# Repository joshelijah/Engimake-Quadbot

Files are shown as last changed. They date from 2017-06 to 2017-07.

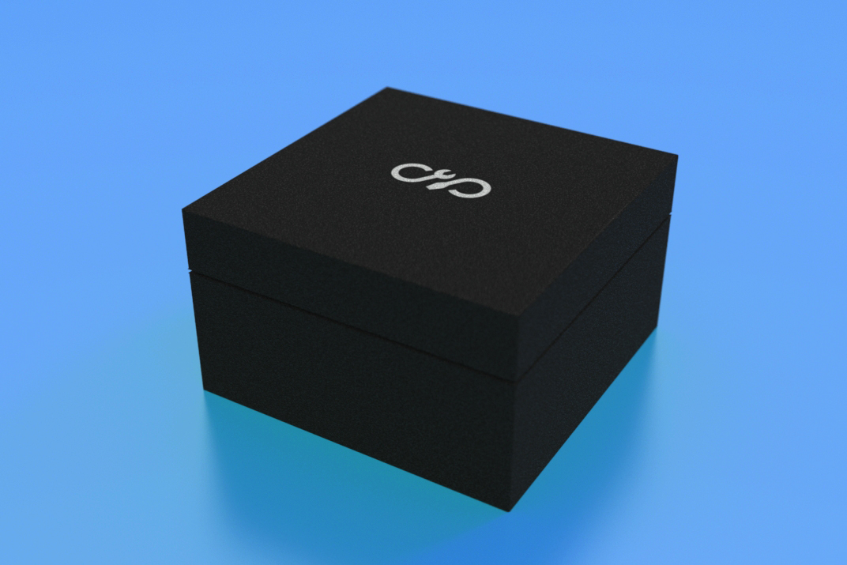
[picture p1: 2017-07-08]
Images/package design mockup.JPG

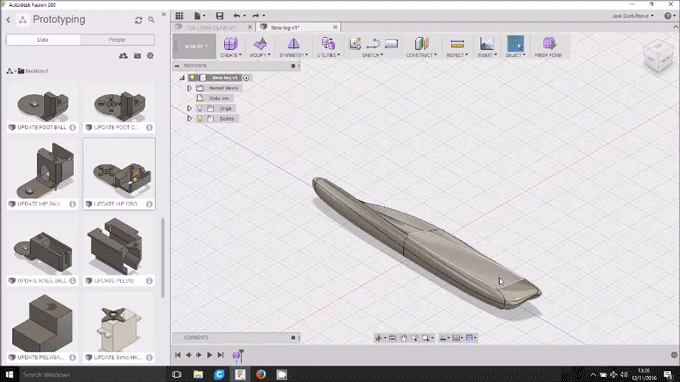
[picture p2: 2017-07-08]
Images/3D-Design.gif

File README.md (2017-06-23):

# Engimake-Quadbot
The design and software files for the Engimake QuadBot. An open source, four-legged, 3D Printed robot. Included here are all the files you'll need to create QuadBot.

1) The Arduino code
2) The Mechanical design files
3) The PCB layout

These files are presented as-is, and are not in a finished state. You'll need to apply initiative to fill in any gaps, this is not a step by step guide! That said these files are the basis of what you'll need to build a working QuadBot.Producing  / manufacturing or creating an object from any of the included design files is expressly at your own risk.

## Getting Started

These instructions will tell you what software you'll need for accessing these design and software files. 

### Prerequisites

What things you need to install the software and how to install them

```
Software: Arduino IDE, found here (www.arduino.cc/en/Main/Software)
Mechanical Design: Any 3D CAD package. We used Autodesk Fusion 360, found here (www.autodesk.com/products/fusion-360/free-trial)
Electronics Design: Any electronics CAD package. We recommend DesignSpark PCB or Eagle (www.rs-online.com/designspark/pcb-software) or (https://www.autodesk.com/products/eagle/free-download)

```

### Installing Arduino

Installing the CAD packages is straight forward. To program QuadBot from Arduino you will need to install Arduino and the following Arduino libraries...

```
1) The Servo library
2) The Adafruit Neopixel library, found here (https://github.com/adafruit/Adafruit_NeoPixel)
3) The QuadBot library, found in these files.
```
The Servo library comes preinstalled with Arduino, and allows us to control the servos. The Adafruit Neopixel library needs to be downloaded and installed to Arduino. Follow the link below for a guide on installing Arduino libraries.

https://www.arduino.cc/en/Guide/Libraries

The QuadBot library was written by us to allow easy programming of QuadBot. It's relatively straight forward and well documented. Credit to Daniel Elijah for writing this fantastic library. d.elijah@gmail.com

```
1) Install the Arduino IDE. 
2) Download the Adafruit Neopixel library and install it.
3) Download the QuadBot library and install it.
```

## Built With

* [Autodesk Fusion 360](www.autodesk.com/products/fusion-360/free-trial) - CAD software
* [DesignSpark PCB](www.rs-online.com/designspark/pcb-software) - Electronics Cad software
* [Arduino](www.arduino.cc/en/Main/Software) - Arduino

## Contributing

Feel free as you wish to contribute your designs. This repository is not maintained.

## Authors

Engimake Ltd.

## License

This project is licensed under the Creative Commons Attribution-ShareAlike 4.0 International License (CC BY-SA 4.0). Refer to http://creativecommons.org/licenses/by-sa/4.0/ for more information.

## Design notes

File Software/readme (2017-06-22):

##QuadBot Library Files

Place these files in your Arduino library file to install the QuadBot.h Arduino library.

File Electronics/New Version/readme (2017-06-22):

Electronics

Included here are the PCB gerber files that will be needed to manufacture a QuadBoard.

Also included is the Bill of Materials for all components on the board.

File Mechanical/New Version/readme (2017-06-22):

Mechanical Files

Find the QuadBot mechanical files here.

All files are suitable for 3D printing. 

All components are in .f3d and .iges format.

We recommend using Autodesk Fusion 360 for the files.

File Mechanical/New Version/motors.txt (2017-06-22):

The motors used for QuadBot are...

Feetech FS90 servo.

You can buy them from multiple places, including...

https://www.pololu.com/product/2818
https://www.rapidonline.com/feetech-fs90r-360-continuous-rotation-micro-servo-37-1335
https://grobotronics.com/servo-micro-1.5kg.cm-plastic-gears-feetech-fs90.html

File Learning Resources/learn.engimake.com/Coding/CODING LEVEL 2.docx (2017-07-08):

LEFT SIDEBAR | MAIN CONTENT
IMAGE
TITLE: CODING LEVEL 2
BLURB: Take your coding knowledge to the next level!
LEFT MENU: The Arduino Environment, The Arduino Language, What is a Library?, Anatomy of an Arduino Sketch, Conclusion

URL: engimake.com/coding/l2/0

The Arduino Environment (H1)

If you want to get set up and running, check out our the getting started guide. Here we’ll learn about the Arduino environment

The Arduino programming language is what we use to program QuadBot. Arduino is a huge platform with a large user base and lots of example code. It forms the core of every program we’ll write for QuadBot.

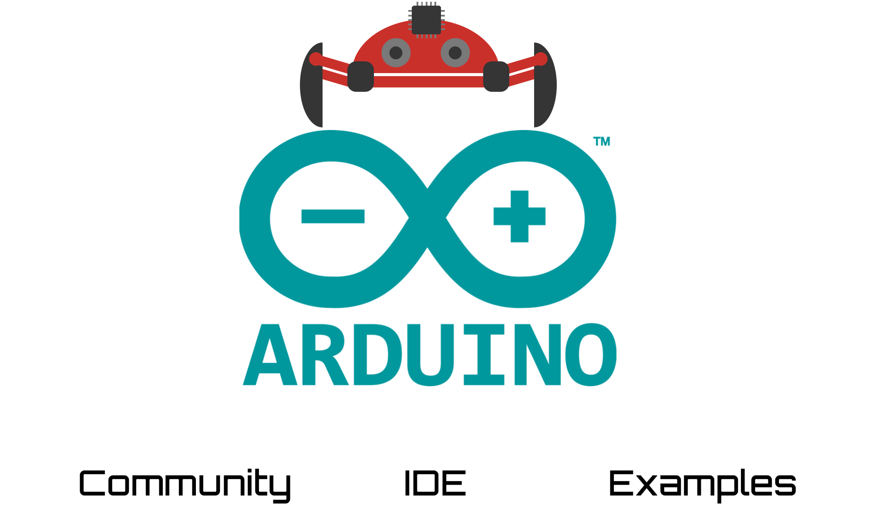
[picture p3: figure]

But what actually is the Arduino language? Let’s take a look.
RIGHT BUTTON TEXT: NONE URL | LEFT BUTTON TEXT: The Arduino Language URL: engimake.com/coding/l2/1

URL: engimake.com/coding/l2/1

The Arduino Language (H1)

Arduino is based on the C++ language, which has been around since 1983. The normal C++ used with microcontrollers but can be a bit complicated.

The Arduino language makes C++ a lot easier because it gives you loads of software libraries containing pre-written functions. This means if you want to perform a specific operation it’s likely there’s a function already existing for you to use.

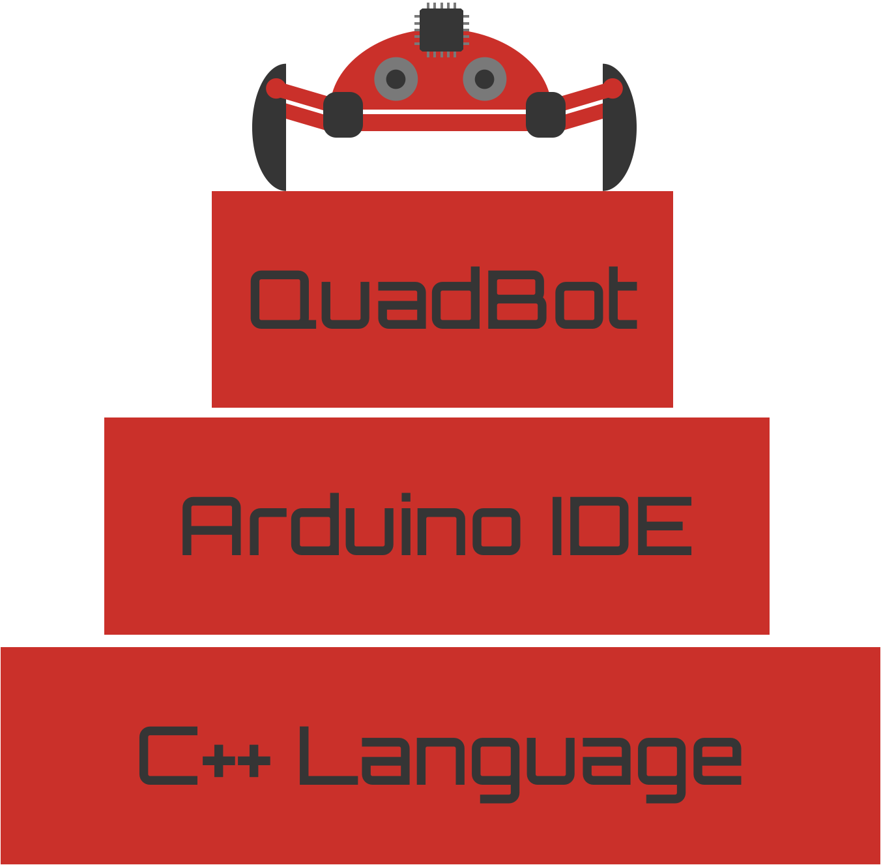
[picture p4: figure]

QuadBot is built from the Arduino Integrated Development Environment (IDE). The Arduino IDE is built from the C++ Language.
RIGHT BUTTON TEXT: The Arduino environment URL: engimake.com/coding/l2/0 | LEFT BUTTON TEXT: What is a library? URL: engimake.com/coding/l2/2

URL: engimake.com/coding/l2/2

What is a Library (H1)

A software library is just a big list of functions written by someone else. They’ve done all the hard work of creating the function and getting it work, so that we can use the function in our programs. Why? Because coders are pretty awesome people.

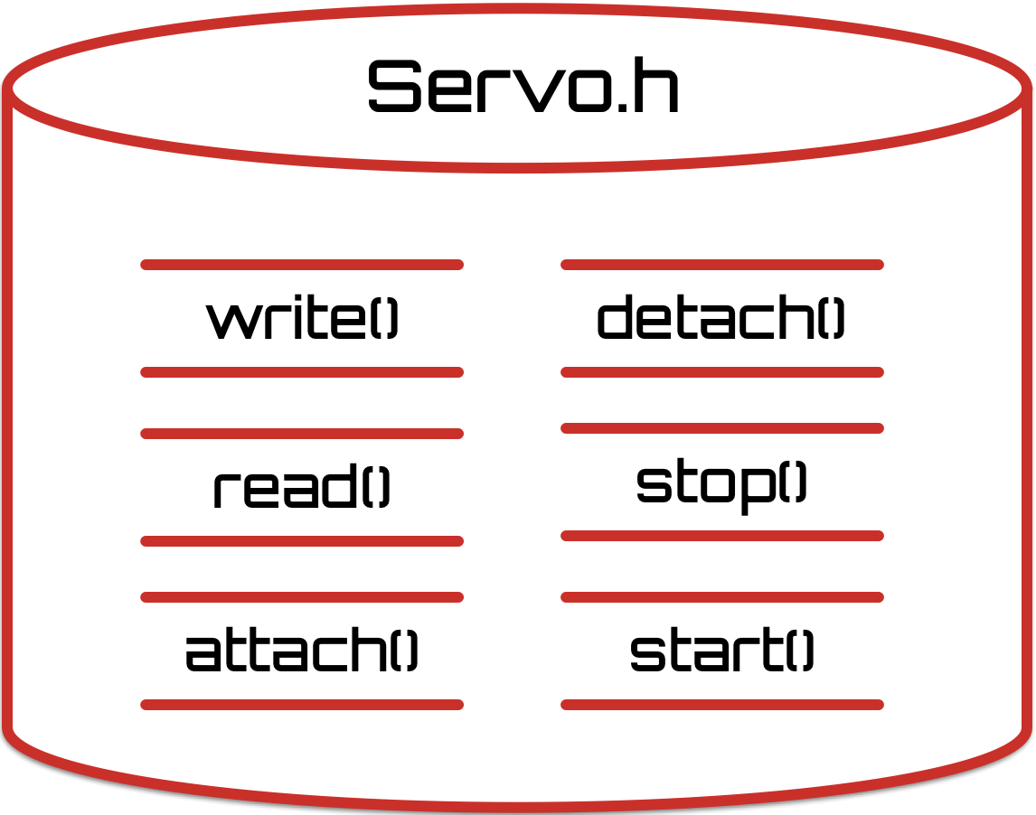
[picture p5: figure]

Think of a library as like a container for a load of functions that all relate to one thing. For example here we’ve got the Servo library, which relates to Servo motors. The library contains functions to stop and start the servo, amongst others.

There are a LOT of different libraries for arduino, some are official and well documented, others are unofficial and bit hacky.

To include a library in our code, we use the following statement at the top of our program…

#include <Servo.h>

RIGHT BUTTON TEXT: The Arduino language URL: engimake.com/coding/l2/1 | LEFT BUTTON TEXT: Anatomy of an Arduino sketch URL: engimake.com/coding/l2/3

URL: engimake.com/coding/l2/3

Anatomy of an Arduino sketch (H1)

All Arduino sketches consist of two parts, setup() and loop(). The setup() runs once at the start, the loop() runs continuously.

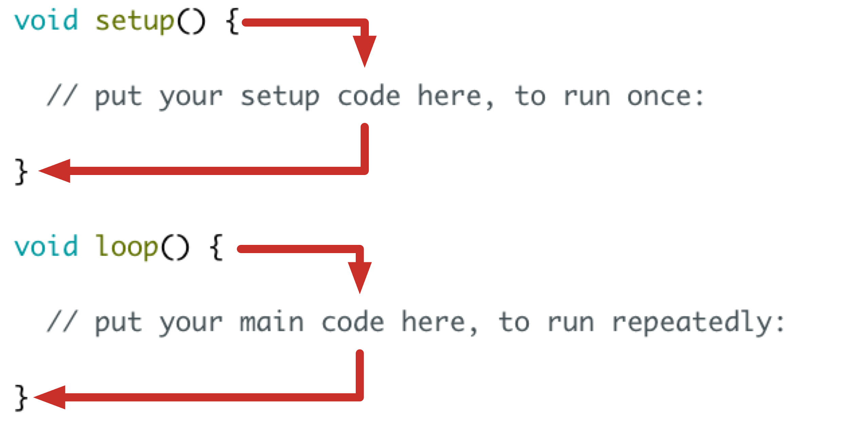
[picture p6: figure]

You’ll use the setup() for things like setting up pins as inputs or outputs. These only happen once. You’ll use the loop() to run your main code.

Here’s an Arduino sketch in all its glory.

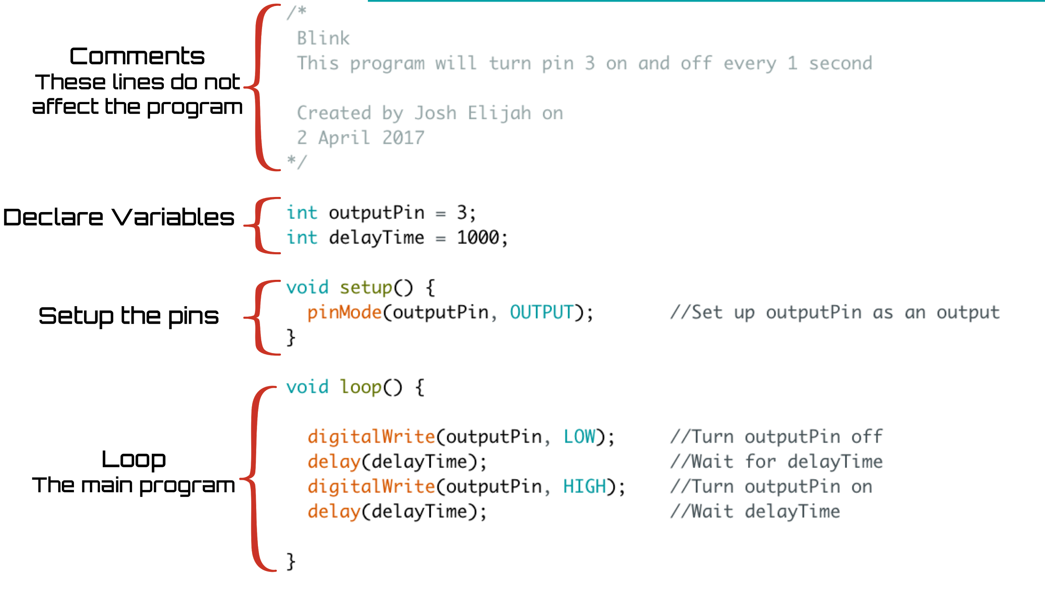
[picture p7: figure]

Comments: These do not affect the program, they are there to help humans understand the code.

Declare Variables: We declare any variables here at the start of the program.

Setup: We setup the pin as an output. We only need to do this once at the start, so it goes in setup().

Loop: Inside here is the code we want to repeat, turning the pin on and off.
RIGHT BUTTON TEXT: What is a library URL: URL: engimake.com/coding/l2/2 | LEFT BUTTON TEXT: Conclusion URL: URL: engimake.com/coding/l2/4

URL: engimake.com/coding/l2/4

Conclusion (H1)

Now you’re getting very familiar with the Arduino language. Continue on to learn more about coding, or head over to our get started guides to get QuadBot moving!
RIGHT BUTTON TEXT: Anatomy of an Arduino sketch URL: engimake.com/coding/l2/3 | LEFT BUTTON TEXT: URL

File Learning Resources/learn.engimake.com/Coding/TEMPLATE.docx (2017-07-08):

LEFT SIDEBAR | MAIN CONTENT | RIGHT SIDEBAR

RIGHT BUTTON TEXT URL | LEFT BUTTON TEXT URL

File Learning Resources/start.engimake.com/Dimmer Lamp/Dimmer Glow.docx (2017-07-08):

Left Sidebar

Create a dimmable lamp with QuadBot

Overview

Analog Input

Reading the Dial

The Map Function

Combining what we know

Difficulty rating: 3

Fun Rating: 3

Time taken: 25 mins

Supporting activity - QuadBot Colour

Dimmer Control

Master analog input and LED control to create a dimmable lamp with QuadBot.

Dimmable LEDs GIF

There’s a handy dial on QuadBot that we can program to control any of features. In this activity you’ll program the dial to control the brightness of LEDs. First let’s look at analog input.

Analog Input

QuadBot can sense analog voltages between 0 volts and 5 volts using its onboard microcontroller. Coincidentally, the dial onboard QuadBot outputs a voltage between 0 volts and 5 volts depending on the position it is in. That means we can use the dial to send different voltages to QuadBot’s microcontroller, allowing us to input a varying value.

Varying voltage from dial photo (with graphic overlay)

The microcontroller reads this voltage as a number between 0 and 1023. 0 volts means 0, and 5 volts means 1023. This might seem a bit strange, and it’s down to how microcontrollers store the voltage information.

Why does a microcontroller read an analog voltage as a number between 0 and 1023? Read our Input and Output tutorial.

Now we know that let’s look at how to actually use this…

Reading the dial

We can use the readDial() function from the QuadBot.h library to return the current value of the dial, like this…

#include <QuadBot.h> //Include the QuadBot Library

int dial; //Declare a variable to store the value of the dial

void setup(){

QuadBot.begin() //Initialize QuadBot

}

void loop(){

dial = QuadBot.readDial() //Read the value of the dial and store it in “dial”

}

The readDial() function returns the value from the dial (between 0 and 1023) We can use this variable in our code to make decisions.

To use this value to control the LED brightness, we’ll need to give the value into the QuadBot.setLEDs(R,G,B) function.

There’s a problem though. We know that readDial() returns a value between 0 and 1023, however we know that setLEDs() expects values for R,G and B between 0 and 255! To solve this problem we can use the map() function...

The Map Function

The Map function is one of those sort of functions you just can’t live without. It’s built into the Arduino environment and you can read about it in detail Arduino’s page here (https://www.arduino.cc/en/reference/map). The map function takes one number from one range, and scales it into another number from another range.

To understand this, let’s take an example. Say I’ve got a grade of 0.73 out of a range between 0 and 1. How can I express that as a grade between 0 and 100. This is simple, we can just multiple the original grade by 100. So 0.73 between 0 and 1 is equivalent to 73 between 0 and 100. That’s a very simple mapping.

But how can we do this for more complicated mappings?

- Map 34 from range 5-85 to range 0 to 100
- Map 0.1 from range -4 to 4 to range 80 to 90
- Map 512 from range 0 to 1023 to range 0 to 255

We could go through the math, but we don’t have to, we can use the Arduino map() function. The function takes five inputs and returns the new, mapped value. We use it like this…

int newVal = map(oldVal, oldLow, oldHigh, newLow, newHigh);

So to map value “dial” in the range of 0 to 1023, to the range of 0 to 255 we do the following.

map(dial, 0, 1023, 0, 255);

Combining what we know

Let’s bring it all together to create our dimmer switch. Let’s read the dial, map the value, then use it to set the LEDs…

#include <QuadBot.h> //Include the QuadBot Library

int dial; //Declare a variable to store the value of the dial

int level; // Declare a variable to store the brightness value

void setup(){

QuadBot.begin() //Initialize QuadBot

}

void loop(){

dial = QuadBot.readDial() //Read the value of the dial and store it in “dial”

level = map(dial, 0,1023, 0,255); //map the value to bet

setLEDs(level, level, level); //Set the brightness according to the level

}

And hurrah! You’ve now created a white dimmer lamp with QuadBot. Try using some maths to increase/decrease the brightness values for R, G and B. That way you can create a colored dimmer lamp!

Conclusion

Now you’re getting somewhere! Well done, you’ve combined input with output and are ready to move on to some more advanced concepts, go you!

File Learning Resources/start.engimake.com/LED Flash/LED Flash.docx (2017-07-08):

Left Sidebar

The Arduino equivalent of “Hello World!”

Overview

Digital Output

Conclusion

Difficulty rating: 1

Fun Rating: 1

Time taken: 10 mins

Dimmer Control

Understand basic programming and digital output by flashing the onboard LED.

Fl LEDs GIF

There’s a small LED on QuadBot that’s hooked up directly to one of the digital pins on the microcontroller. In this most simple exercise let’s make it flash

There’s a handy dial on QuadBot that we can program to control any of features. In this activity you’ll program the dial to control the brightness of LEDs. First let’s look at analog input.

Digital Output

There are two voltage levels when it comes to a digital output pin, High and Low. High means 5V and Low means 0V on QuadBot. When the digital pin 3 is high, an LED on QuadBot turns on. When digital pin 3 is low, the LED turns off. Simples.

What is a digital signal? Read our Input and Output tutorial.

To toggle the voltage on this pin we can use the digitalWrite() function like this…

void setup(){

pinMode(3, OUTPUT);

}

void loop(){

digitalWrite(3, HIGH); //Send out a HIGH on digital pin 3

digitalWrite(3, LOW); //Send out a HIGH on digital pin 3

}

You expect to see the LED flashing right? But if you tried it, you’d see that the LED is constantly on? Why?

Well the microcontroller runs very quickly at up to 16 million operations per second. That means that even though the LED is being turned on and off, it is so quick we can’t see it. To solve this let’s use the delay() function to make the microcontroller wait between each toggle..

void setup(){

pinMode(3, OUTPUT);

}

void loop(){

digitalWrite(3, HIGH); //Send out a HIGH on digital pin 3

delay(1000); //Wait for 1 second

digitalWrite(3, LOW); //Send out a HIGH on digital pin 3

delay(1000); //Wait for 1 second

}

Now you’ll see a second delay between each toggle. Try changing the delay times and see what it does to the flashing LED.

Conclusion

Now that’s a start. That’s your most basic microcontroller introduction. Now move onto something more exciting!

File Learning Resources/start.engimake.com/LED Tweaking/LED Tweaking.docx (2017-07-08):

Left Sidebar

Let’s tweak the LEDs one by one to get custom patterns

Overview

Editing our motor tweak code

Difficulty rating: 4

Fun Rating: 4

Time taken: 25 mins

Supporting activity - Motor Tweaking

LED Tweaking

Get manual control over all the LEDs and be able to tweak them individually using the dial.

LED tweaking

Let’s adapt our motor tweaking code to tweak each LED individually...

Editing our motor Tweak code

This is very simple, let’s simply replace the motor code with LED code...

int newButtonState = LOW;

int oldButtonState = LOW;

int numberOfPresses = 0;

int LEDnumber = 0;

int dial;

long color;

void setup() {

QuadBot.begin();

}

void loop() {

newButtonState = QuadBot.readButton(); //Read the value of button

if (newButtonState != oldButtonState) { //If the button is different to its previous value…

if(newButtonState == LOW){ //If the button has just been pressed, the value should be LOW

numberOfPresses++; //Increment the number of presses

}

}

delay(50);

oldButtonState = newButtonstate; //Assign the current button state to be the old button state for the next loop.

LEDnumber = numberOfPresses%8 //Take the modulo 8 of numberOfPresses

dial = map(QuadBot.readDial(),0,1023,0,255);

color = colorWheel(dial);

QuadBot.writeLED(LEDnumber, angle); //Set the angle of the motor to the mapped dial value

}

And that’s it, the same as before but now with LEDs

Conclusion

Very simple, let’s move on!

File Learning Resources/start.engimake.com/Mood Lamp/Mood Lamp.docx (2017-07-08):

Left Sidebar

Add color control to your dimmable QuadBot lamp.

Overview

Reading the button and setting the color

Setting the brightness

Difficulty rating: 3

Fun Rating: 4

Time taken: 25 mins

Supporting activity - QuadBot Color

Color Controlled Dimmer

Upgrade the dimmable QuadBot lamp so that you can control not only the brightness, but the color as well.

Dimmable and Color variable LEDs GIF

We’ll combine using the dial and the button on QuadBot to let use the dial to set either the brightness or the color of the QuadBot. First let’s adapt our previous code to make the color change only when the button is pressed.

Add button read into our previous code

We can use the readButton() function to decide whether to change the color of the LEDs. We use a new function here called colorWheel() that converts a number from 0 to 255 into a color on the color wheel.

#include <QuadBot.h> //Include the QuadBot Library

long color; //A variable to store the color value

int dial; //A variable to store the value of the dial

void setup(){

QuadBot.begin() //Initialize QuadBot

}

void loop(){

dial = map(analogRead(A0),0,1023,0,255); //Map dial value to maximum 255

if(QuadBot.readButton()){ //If the button is pressed

color = colorWheel(dial); //Set dial to be the colorwheel position of dial

writeLEDs(color); //Set the color of the LEDs using the color wheel

}

}

Now whenever you press the button, you should be able to change the color by turning the dial!

Setting the brightness

Finally let’s make the dial control the LED brightness when the button isn’t pressed. We can just add an else statement to our code, that runs when the button isn’t pressed!

#include <QuadBot.h> //Include the QuadBot Library

long color; //A variable to store the color value

int dial; //A variable to store the value of the dial

void setup(){

QuadBot.begin() //Initialize QuadBot

}

void loop(){

dial = map(analogRead(A0),0,1023,0,255); //Map dial value to maximum 255

if(QuadBot.readButton()){ //If the button is pressed

color = colorWheel(dial); //Set dial to be the colorwheel position of dial

writeLEDs(color); //Set the color of the LEDs using the color wheel

}

else{

setLEDsBrightness(dial); //Set the brightness of the LEDs

}

delay(1) //Add a small loop delay

}

And now you should be able to get the exact color and brightness you want on QuadBot! Great work!

Conclusion

Fantastic progress! You’re starting to combine multiple inputs and make decisions for outputs. This is the essense of robotics! Let’s try some of the other outputs on QuadBot!

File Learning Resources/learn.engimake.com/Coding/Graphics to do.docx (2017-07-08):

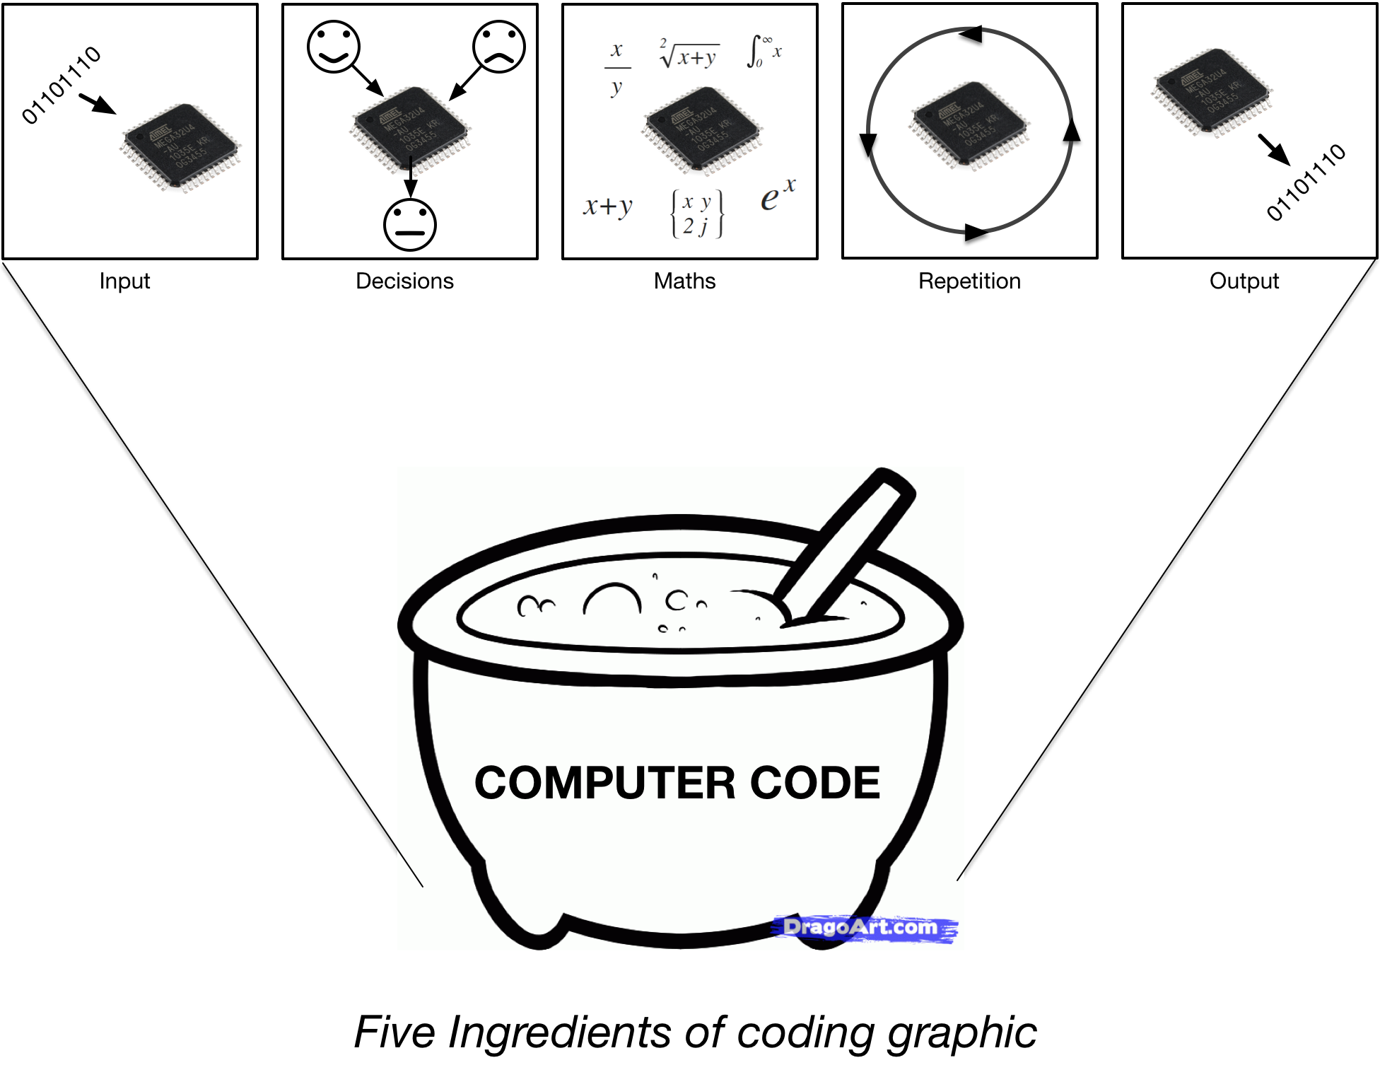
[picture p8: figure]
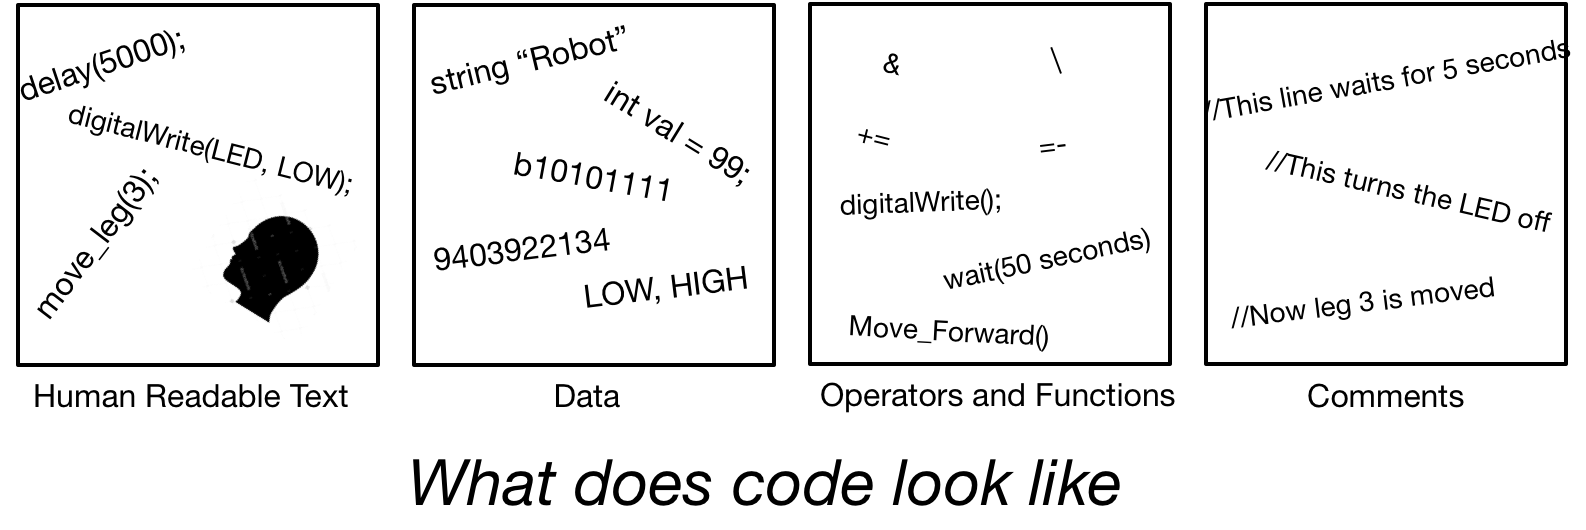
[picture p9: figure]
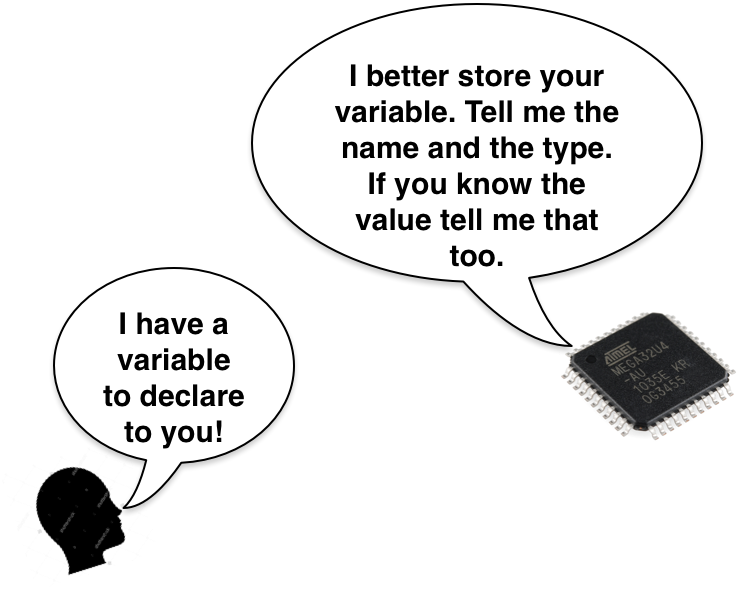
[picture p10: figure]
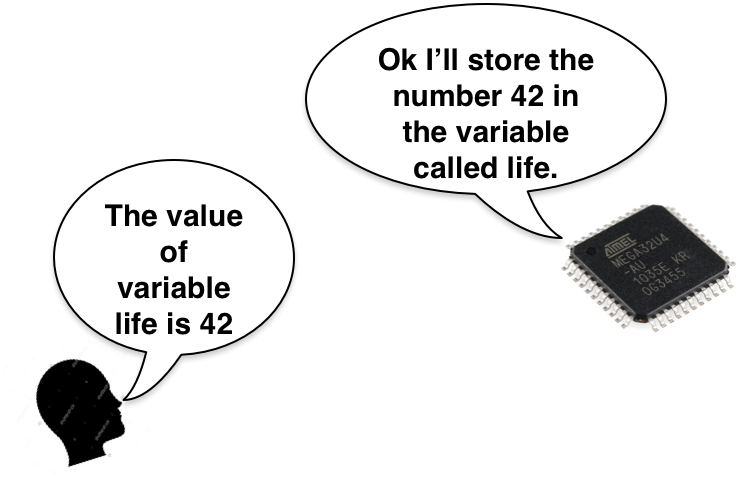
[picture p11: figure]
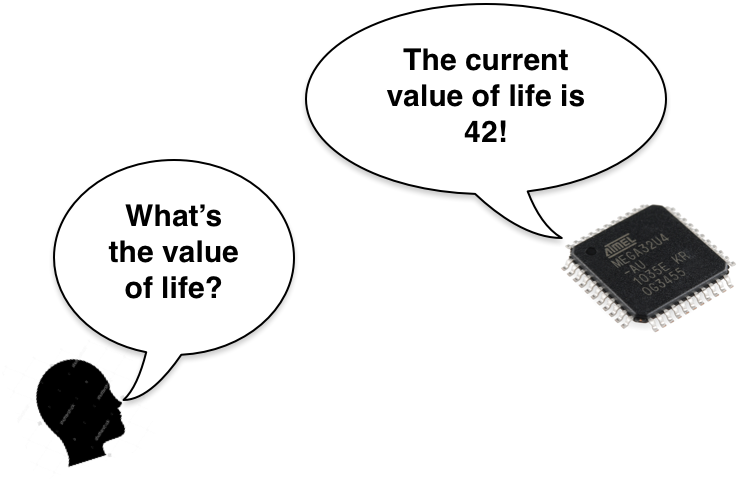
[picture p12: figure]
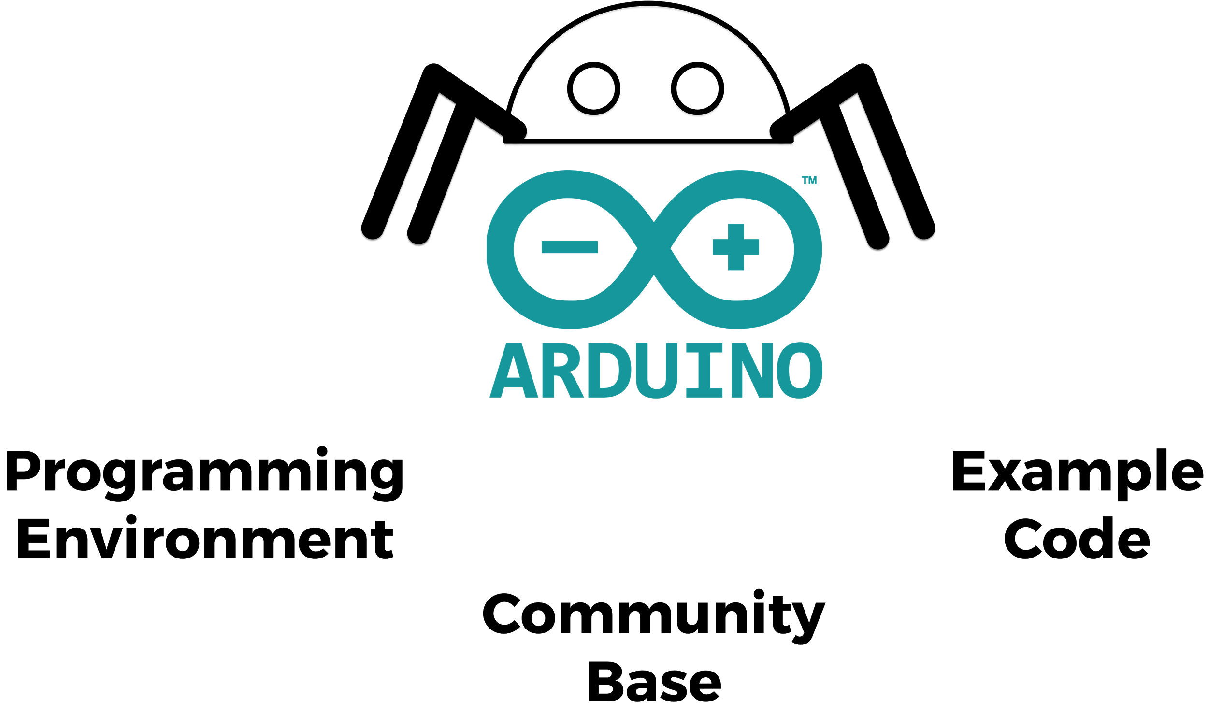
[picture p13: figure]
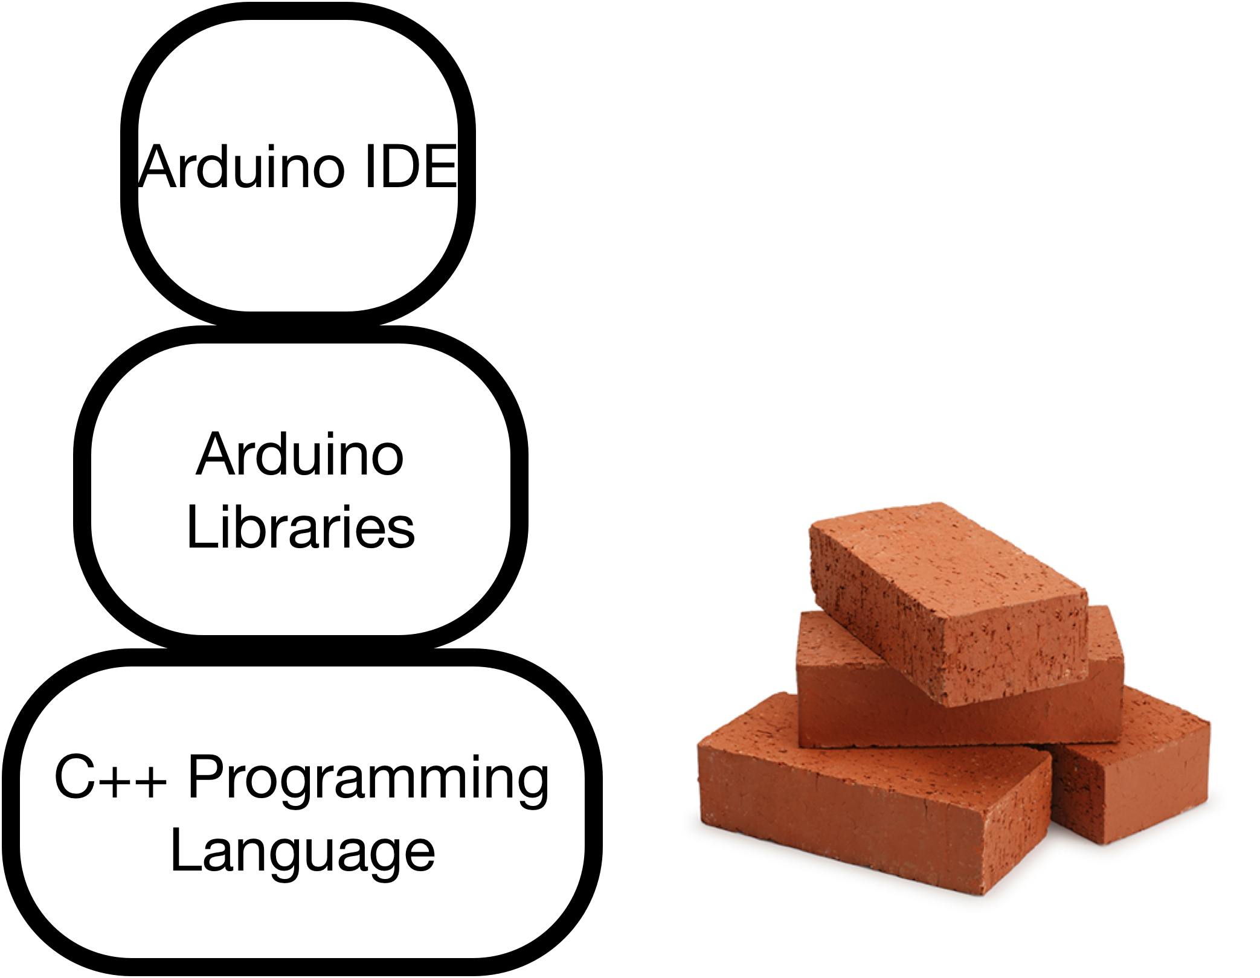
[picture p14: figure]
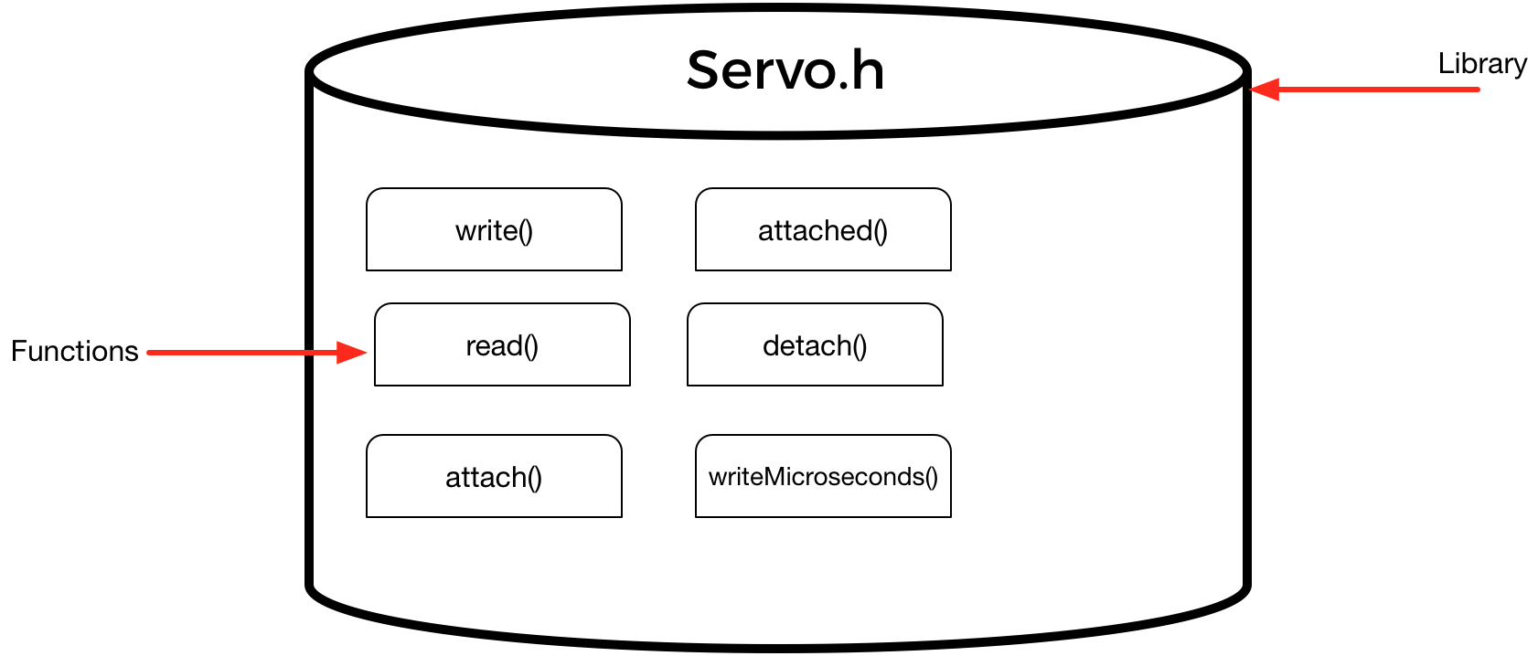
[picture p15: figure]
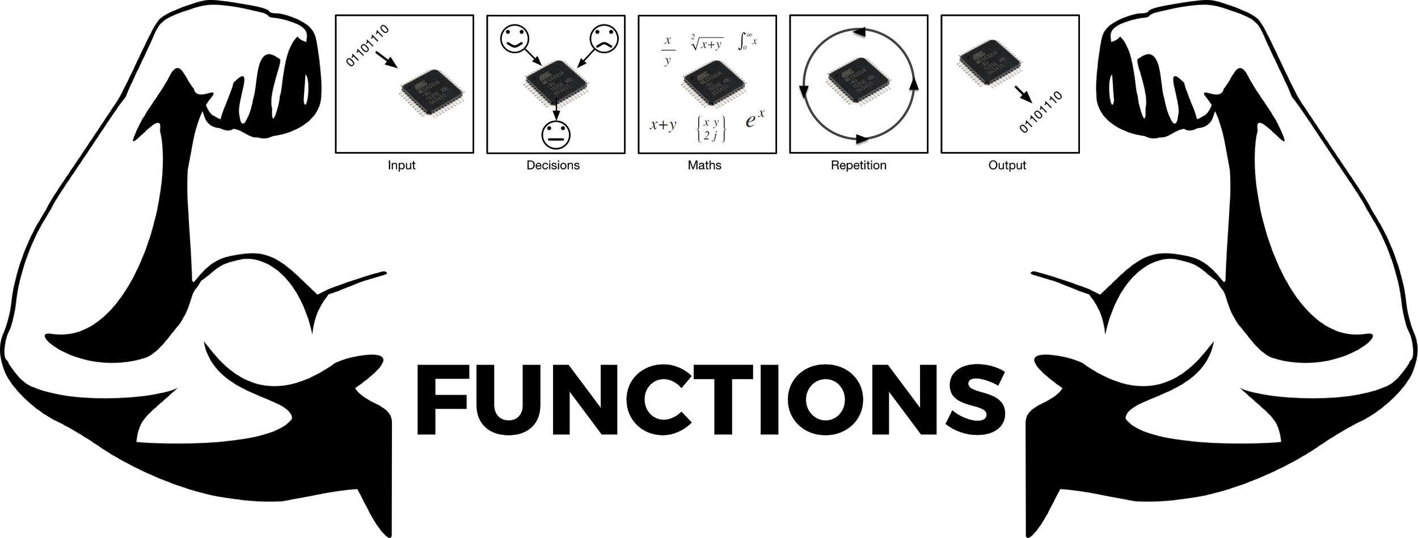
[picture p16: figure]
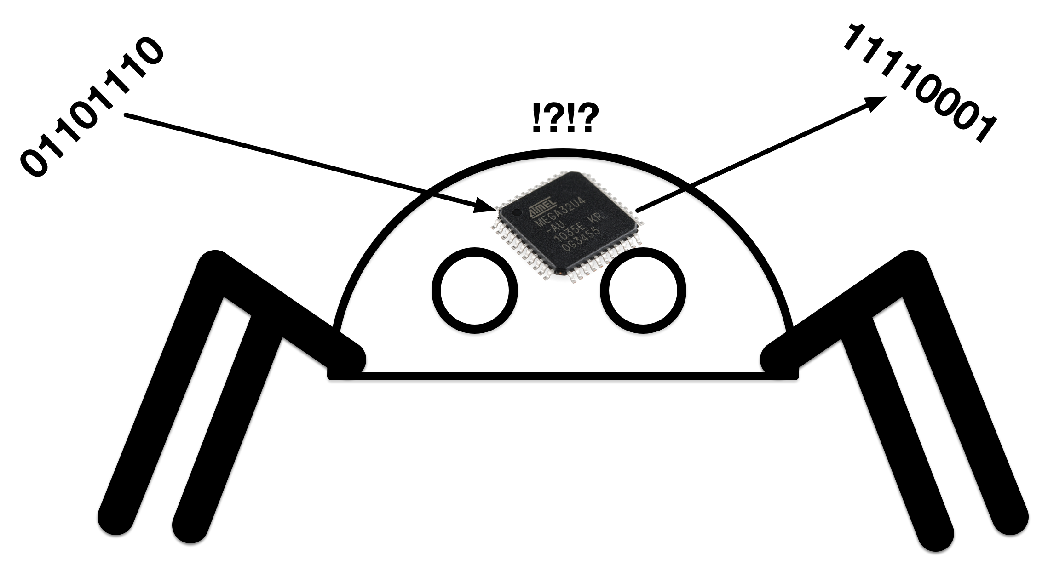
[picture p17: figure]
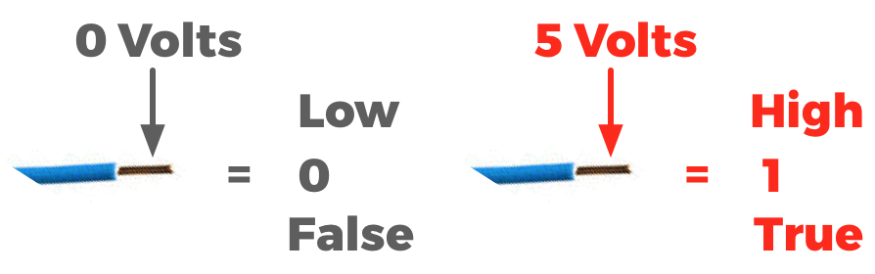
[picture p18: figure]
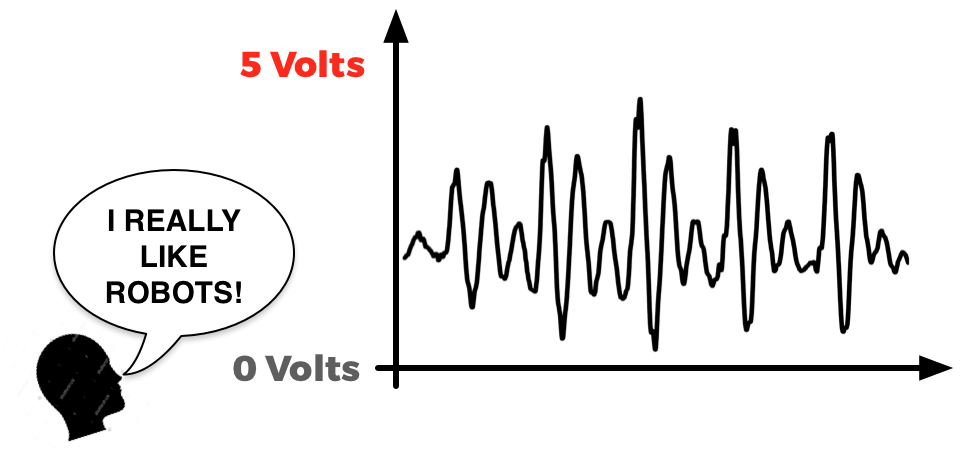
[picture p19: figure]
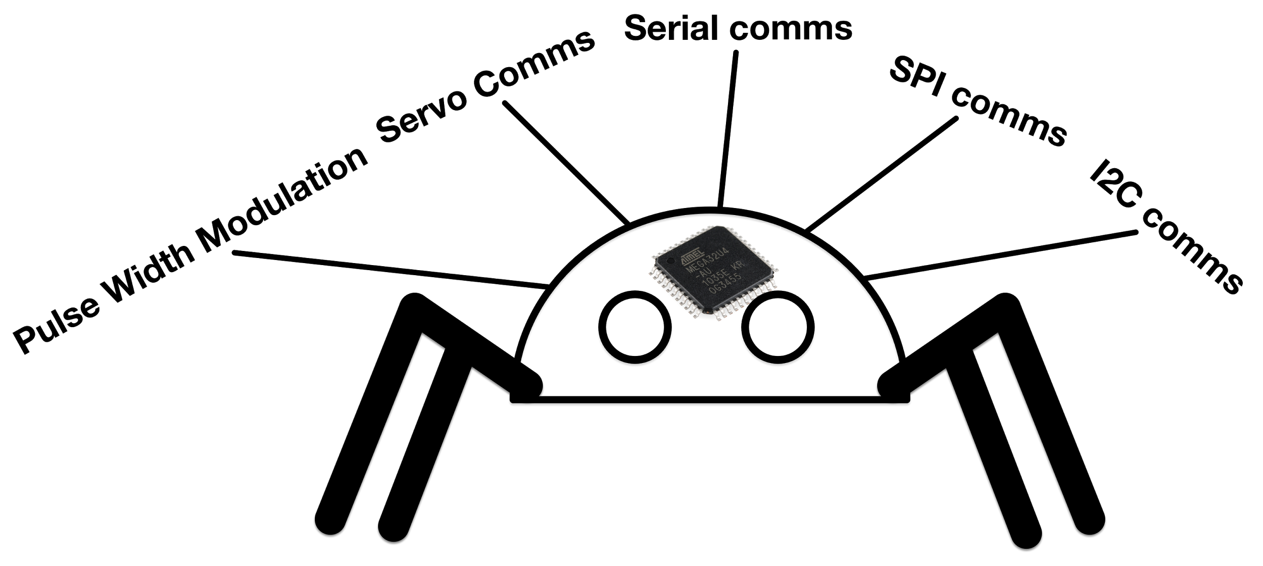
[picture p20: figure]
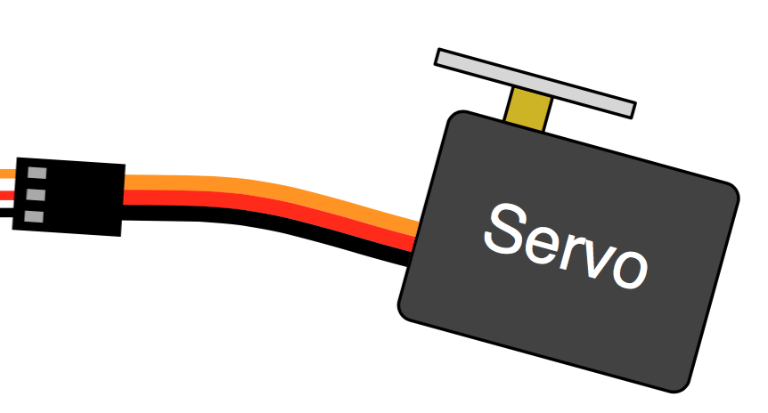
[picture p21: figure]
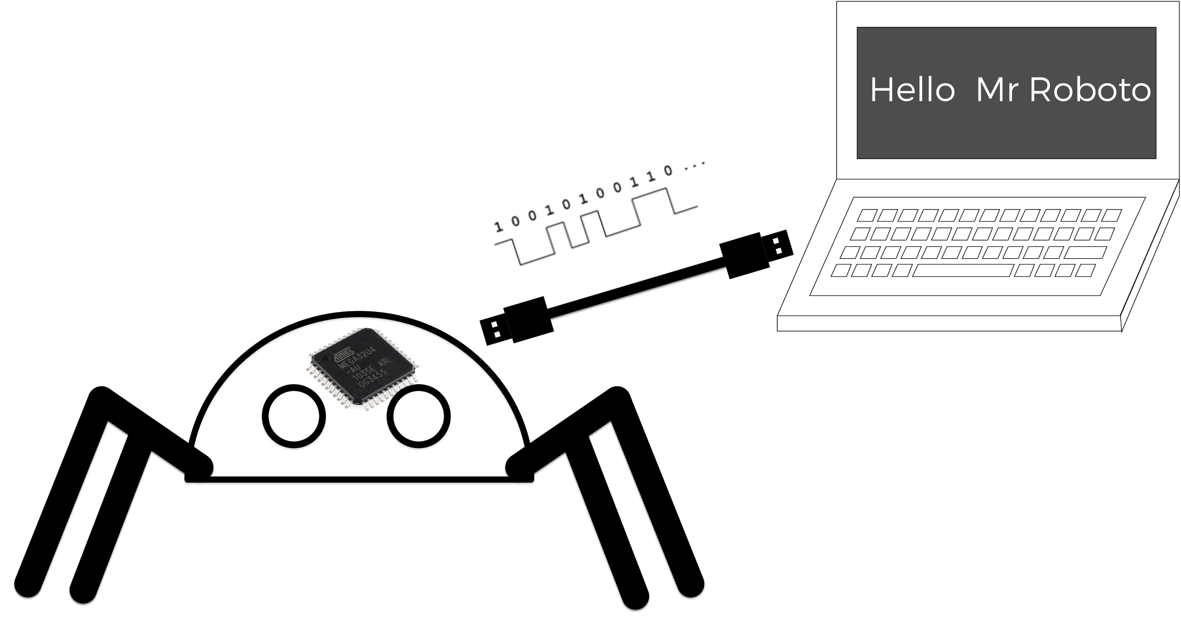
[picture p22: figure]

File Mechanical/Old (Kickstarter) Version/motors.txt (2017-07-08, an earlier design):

The motors used for the Kickstarter QuadBot are...

HobbyKing™ HK15178B Digital Servo MG 1.5kg / 0.08sec / 13.5g.

You can buy them from hobby king

https://hobbyking.com/en_us/hobbykingtm-hk15178b-digital-servo-mg-1-5kg-0-08sec-13-5g.html

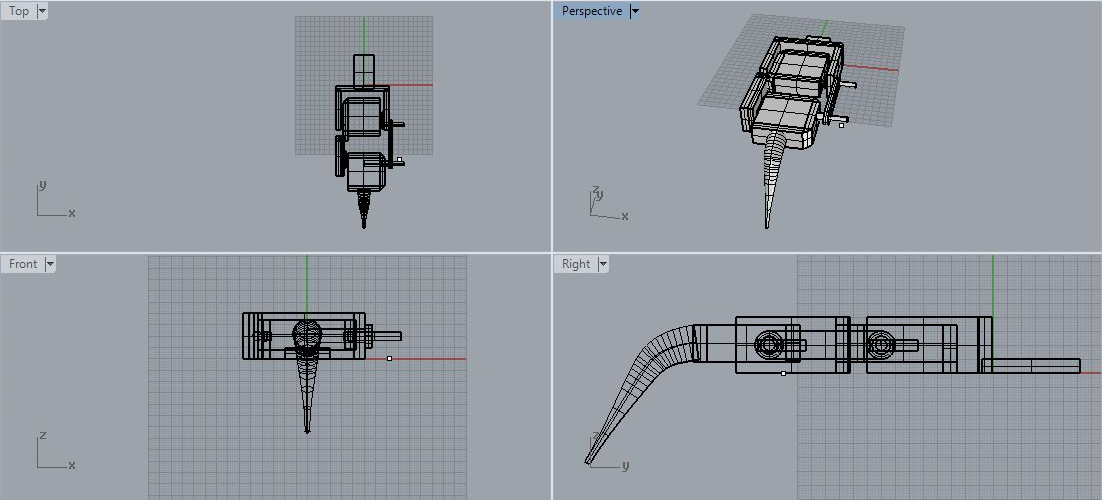
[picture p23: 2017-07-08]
Images/quadbot leg 3D design.png

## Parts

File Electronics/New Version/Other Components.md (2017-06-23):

1 x 18650 battery

1 x Cross head screwdriver

1 x Pliers OR Wrench (for M3 nut only)

1 x USB (Micro-B)

26 x NUT, M3, NYLOCK (special kind with an embedded nylon washer)

26 x BOLT, M3, 40mm

8 x NUT, M2

8 x BOLT, M2, 10mm

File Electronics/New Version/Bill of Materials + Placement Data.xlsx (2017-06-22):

#Board Size is 3718.363804 x 3543.270546.
#
#Placement Data:
#Designator | X-Loc | Y-Loc | Rotation | Side | Type | X-Size | Y-Size | Value | Footprint | Populate
BT1 | 1769.67 | 1770.26 | 0 | 2 | 2 | 2898.43 | 55.51 | 18650HOLDER | 18650HOLDER | 1
C1 | 470.06 | 1889.75 | 180 | 1 | 1 | 62.99 | 23.62 | 1u | C0402 | 1
C2 | 458.56 | 2446.12 | 270 | 1 | 1 | 62.99 | 23.62 | 1u | C0402 | 1
C3 | 2328.13 | 1655.3 | 90 | 1 | 1 | 62.99 | 23.62 | 1u | C0402 | 0
C4 | 797.62 | 1450.77 | 270 | 1 | 1 | 62.99 | 23.62 | 1u | C0402 | 1
C5 | 649.59 | 1449.98 | 270 | 1 | 1 | 62.99 | 23.62 | 1u | C0402 | 1
C6 | 1062.19 | 1772.82 | 90 | 1 | 1 | 62.99 | 23.62 | 1u | C0402 | 1
C7 | 1125.97 | 1771.64 | 90 | 1 | 1 | 82.68 | 35.43 | 10u | C0603 | 1
C8 | 1102.34 | 1975.57 | 270 | 1 | 1 | 82.68 | 35.43 | 10u | C0603 | 1
C9 | 1658.64 | 1523.21 | 0 | 1 | 1 | 62.99 | 23.62 | 27p | C0402 | 1
C10 | 1927.15 | 1523.21 | 180 | 1 | 1 | 62.99 | 23.62 | 27p | C0402 | 1
C11 | 1870.06 | 2015.73 | 270 | 1 | 1 | 62.99 | 23.62 | 1u | C0402 | 1
C12 | 1496.04 | 1787.38 | 0 | 1 | 1 | 62.99 | 23.62 | 1u | C0402 | 1
C13 | 2283.45 | 2452.74 | 180 | 1 | 1 | 62.99 | 23.62 | 1u | C0402 | 1
C14 | 1601.95 | 2005.49 | 0 | 1 | 1 | 62.99 | 23.62 | 1u | C0402 | 1
C15 | 1004.31 | 1772.82 | 90 | 1 | 1 | 62.99 | 23.62 | 0.1u | C0402 | 1
DIAL | 1771.64 | 2263.76 | 0 | 1 | 2 | 236.22 | 39.37 | BIGPOT | LARGEPOT | 1
F1 | 421.24 | 1993.68 | 0 | 1 | 1 | 157.48 | 110.24 | 1210PTCFUSE | 1210PTCFUSE | 1
F2 | 1171.24 | 1584.63 | 0 | 1 | 1 | 224.41 | 125.98 | MF-MSMF110 | MSMF-STYLE1 | 1
J1 | 106.18 | 1771.64 | 270 | 1 | 1 | 314.96 | 170.28 | MF-CON-MICROUSB-RIGHT | MICROUSB-RIGHT | 1
J2 | 1472.43 | 1503.82 | 270 | 1 | 1 | 131 | 81 |  | TC2030-MCP-NL | 0
J3 | 1928.72 | 1232.66 | 180 | 1 | 2 | 340 | 50 |  | 1X04_LOCK | 1
J4 | 1553.52 | 1236.2 | 180 | 1 | 2 | 240 | 50 |  | 1X03_LOCK | 1
JP1 | 856.52 | 202.98 | 225 | 2 | 2 | 240 | 40 |  | 1X03 | 0
JP2 | 2689.51 | 199.43 | 315 | 2 | 2 | 240 | 40 |  | 1X03 | 0
JP3 | 2060.61 | 1447.62 | 90 | 1 | 2 | 140 | 40 |  | 1X02 | 1
JP4 | 2688.33 | 3343.05 | 45 | 2 | 2 | 240 | 40 |  | 1X03 | 0
JP5 | 857.31 | 3343.05 | 135 | 2 | 2 | 240 | 40 |  | 1X03 | 0
L1 | 1261.79 | 1956.67 | 0 | 1 | 1 | 110.24 | 78.74 | 3.3u | 3.3UIND | 1
L4 | 3671.24 | 1771.64 | 90 | 1 | 1 | 181.1 | 43.31 | VSMY2943SL | VSMYIRLED | 1
LED1 | 980.3 | 2145.65 | 180 | 1 | 1 | 141.73 | 49.21 |  | LED0805 | 1
LED2 | 1413.37 | 2035.41 | 180 | 1 | 1 | 141.73 | 49.21 |  | LED0805 | 1
LED3 | 980.3 | 1397.62 | 0 | 1 | 1 | 141.73 | 49.21 |  | LED0805 | 1
LED4 | 2362.19 | 2035.41 | 180 | 1 | 1 | 141.73 | 49.21 |  | LED0805 | 1
LS1 | 1771.64 | 879.9 | 90 | 2 | 2 | 236.22 | 39.37 | PIEZO | PIEZO12MM | 1
ON | 268.49 | 2453.33 | 190 | 1 | 2 | 94.49 | 464.57 | 500SSP1S2M2QEA | 500SSP1S2M2QEA | 1
PROTECTSHORT | 2852.15 | 1908.25 | 0 | 1 | 1 | 60.43 | 50 |  | SJ_2S-NO | 0
Q1 | 3345.26 | 2066.12 | 90 | 1 | 1 | 114.17 | 106.3 | MF-DSC-SOT233-BSS138 | SOT-23-3 | 1
R1 | 452.74 | 1567.3 | 0 | 1 | 1 | 62.99 | 23.62 | 22R | R0402 | 1
R2 | 452.34 | 1630.3 | 0 | 1 | 1 | 62.99 | 23.62 | 22R | R0402 | 1
R3 | 2527.54 | 1633.84 | 270 | 1 | 1 | 62.99 | 23.62 | 10K | R0402 | 0
R4 | 2637.78 | 1771.64 | 0 | 1 | 1 | 62.99 | 23.62 | 1k | R0402 | 0
R5 | 2527.54 | 1913.37 | 270 | 1 | 1 | 62.99 | 23.62 | 10K | R0402 | 0
R6 | 2307.07 | 1772.03 | 0 | 1 | 1 | 62.99 | 23.62 | 100R | R0402 | 0
R7 | 2161.4 | 2015.73 | 90 | 1 | 1 | 62.99 | 23.62 | 1k | R0402 | 1
R8 | 916.12 | 1963.37 | 180 | 1 | 1 | 102.36 | 51.18 | 2K | R0805 | 1
R9 | 1795.26 | 1523.6 | 180 | 1 | 1 | 62.99 | 23.62 | 1M | R0402 | 1
R10 | 1955.89 | 2015.73 | 270 | 1 | 1 | 62.99 | 23.62 | 10K | R0402 | 1
R11 | 1417.7 | 2198.8 | 180 | 1 | 1 | 62.99 | 23.62 | 22R | R0402 | 1
R12 | 942.89 | 2068.09 | 180 | 1 | 1 | 62.99 | 23.62 | 1k | R0402 | 1
R13 | 1394.86 | 2112.78 | 0 | 1 | 1 | 62.99 | 23.62 | 1k | R0402 | 1
R14 | 934.23 | 1483.84 | 0 | 1 | 1 | 62.99 | 23.62 | 1k | R0402 | 1
R15 | 1942.89 | 978.33 | 180 | 1 | 1 | 62.99 | 23.62 | 1M | R0402 | 1
R16 | 3146.44 | 1388.56 | 90 | 1 | 1 | 62.99 | 23.62 | 1M | R0402 | 1
R17 | 2845.26 | 2164.55 | 270 | 1 | 1 | 102.36 | 51.18 | 100R | R0805 | 1
R18 | 2930.3 | 2164.16 | 270 | 1 | 1 | 102.36 | 51.18 | 100R | R0805 | 1
R19 | 3015.34 | 2164.94 | 270 | 1 | 1 | 102.36 | 51.18 | 100R | R0805 | 1
R20 | 3168.09 | 1508.64 | 0 | 1 | 1 | 62.99 | 23.62 | 470 | R0402 | 1
R21 | 3099.67 | 2164.98 | 270 | 1 | 1 | 102.36 | 51.18 | 100R | R0805 | 1
R22 | 3184.51 | 2164.59 | 270 | 1 | 1 | 102.36 | 51.18 | 100R | R0805 | 1
RST | 917.3 | 1771.64 | 0 | 1 | 2 | 40 | 40 |  | 1X01NS-KIT | 1
RV1 | 359.43 | 1608.25 | 180 | 1 | 1 | 47.24 | 19.69 | NEWVARISTOR | 0402VAR | 1
RV2 | 359.43 | 1544.47 | 180 | 1 | 1 | 47.24 | 19.69 | NEWVARISTOR | 0402VAR | 1
S2 | 3418.49 | 1771.64 | 90 | 1 | 1 | 374.02 | 244.09 | MF-SW-TACT-6MM | TACT6MM | 1
U$1 | 1175.73 | 520.22 | 225 | 2 | 2 | 547.24 | 47.24 | 6WAY | 6WAY | 1
U$2 | 3594.47 | 1772.42 | 180 | 2 | 2 | 35.43 | 135.43 | KM-4457P3C | IRRECTH | 1
U$3 | 2371.08 | 517.47 | 315 | 2 | 2 | 547.24 | 47.24 | 6WAY | 6WAY | 1
U$4 | 2368.33 | 3027.38 | 45 | 2 | 2 | 547.24 | 47.24 | 6WAY | 6WAY | 1
U$5 | 1175.73 | 3024.62 | 135 | 2 | 2 | 547.24 | 47.24 | 6WAY | 6WAY | 1
U$9 | 1256.48 | 2286.6 | 180 | 1 | 2 | 177.56 | 27.56 | SK6812 | SK6812B | 1
U$10 | 1256.08 | 1255.89 | 0 | 1 | 2 | 177.56 | 27.56 | SK6812 | SK6812B | 1
U$11 | 2286.4 | 2286.6 | 180 | 1 | 2 | 177.56 | 27.56 | SK6812 | SK6812B | 1
U$12 | 2286.4 | 1256.67 | 0 | 1 | 2 | 177.56 | 27.56 | SK6812 | SK6812B | 1
U1 | 3000.38 | 1771.83 | 90 | 1 | 1 | 91.34 | 129.92 | RQ3E160ADTB | MOSFETN1CHANNEL | 1
U2 | 2475.57 | 1772.42 | 90 | 1 | 1 | 96.46 | 149.61 | DWO1A | SOT23-6 | 0
U3 | 2795.45 | 1771.64 | 270 | 1 | 1 | 133.86 | 92.52 | ECH8693R | SOT-28FL | 0
U4 | 723.8 | 1775.97 | 180 | 1 | 1 | 171 | 236.61 | TP4056 | SOP8 | 1
U5 | 1260.61 | 1771.24 | 180 | 1 | 1 | 120.08 | 68.9 | DIO6605B | DFN2*3-8 | 1
U6 | 1771.64 | 1771.64 | 0 | 1 | 1 | 287.4 | 287.4 | ATMEGA32U4-XUMU | QFN44ML7X7 | 1
X1 | 1794.47 | 1401.95 | 0 | 1 | 1 | 358.27 | 47.24 | NEWCRYSTAL | ABLS7M2-16.000MHZ-D-2Y-T | 1

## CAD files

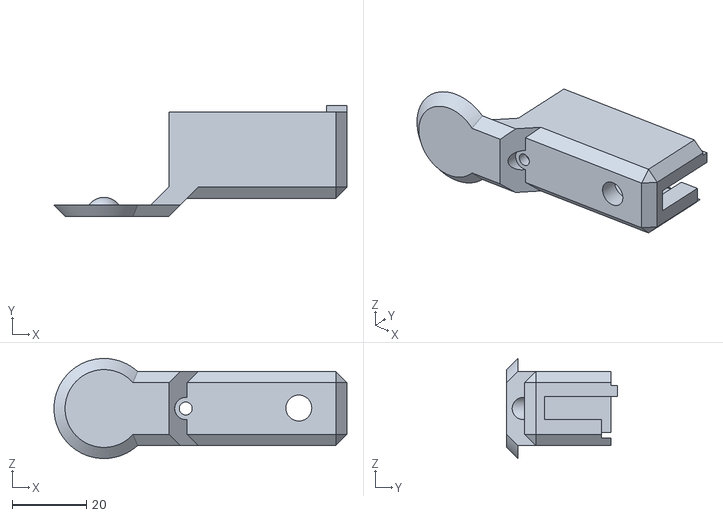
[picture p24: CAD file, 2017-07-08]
Images/QuadBot Iteration 6 (Update) (with colours)/4 x Knee Ball (BLACK).stl
79.1 x 29.9 x 27.0

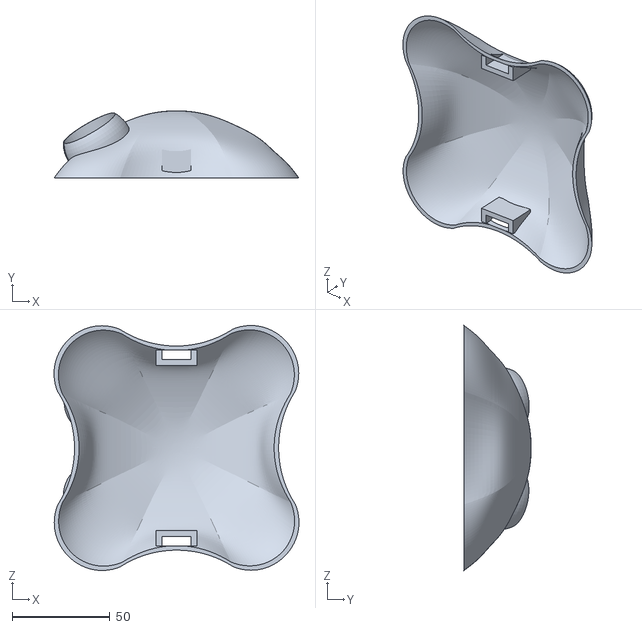
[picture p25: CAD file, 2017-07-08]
Images/QuadBot Iteration 6 (Update) (with colours)/1 x Shell (WHITE).stl
125.4 x 34.5 x 125.4

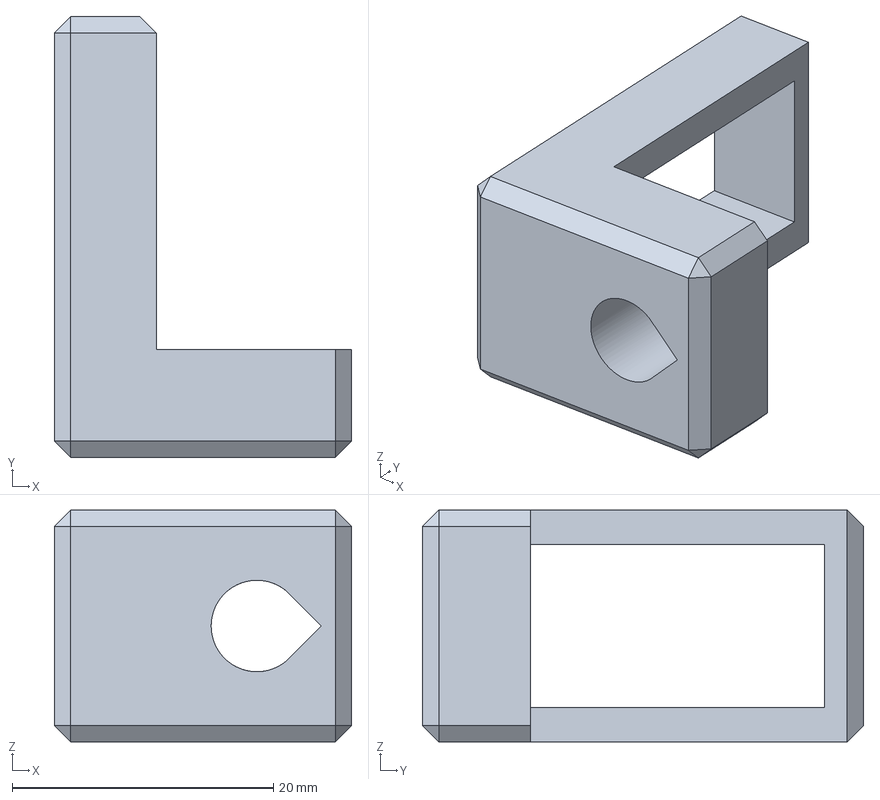
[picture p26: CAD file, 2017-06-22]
Mechanical/New Version/Components/Pelvis (x4).iges
22.8 x 33.8 x 17.8 mm

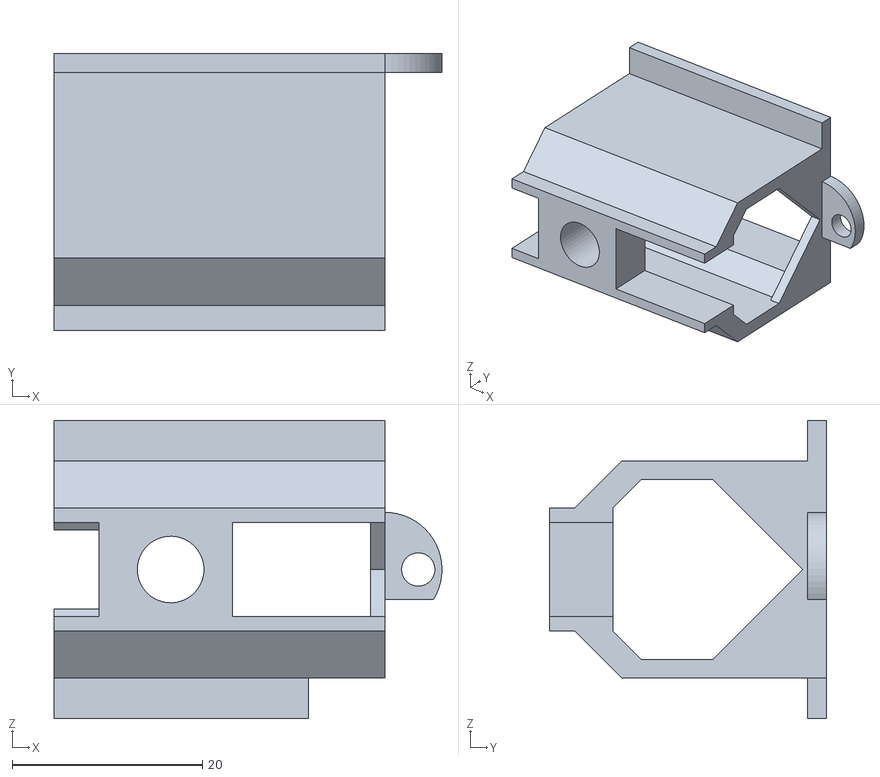
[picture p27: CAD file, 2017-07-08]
Images/QuadBot Iteration 6 (Update) (with colours)/4 x Pelvis (BLACK).stl
40.7 x 29.1 x 31.3

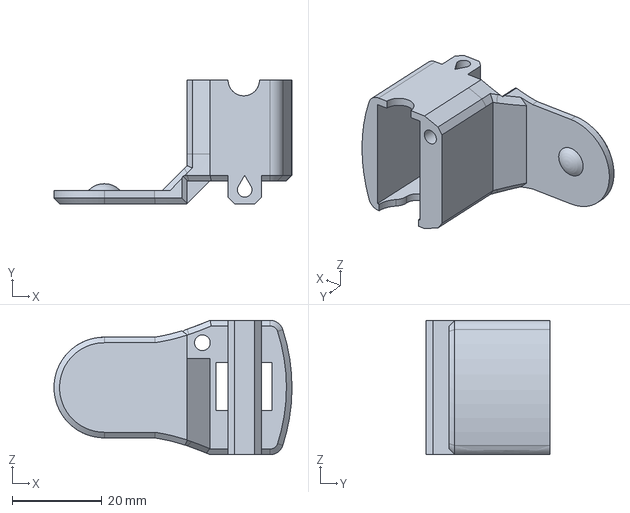
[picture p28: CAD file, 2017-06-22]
Mechanical/New Version/Components/Hip Ball (x4).iges
53.2 x 27.6 x 30.0 mm

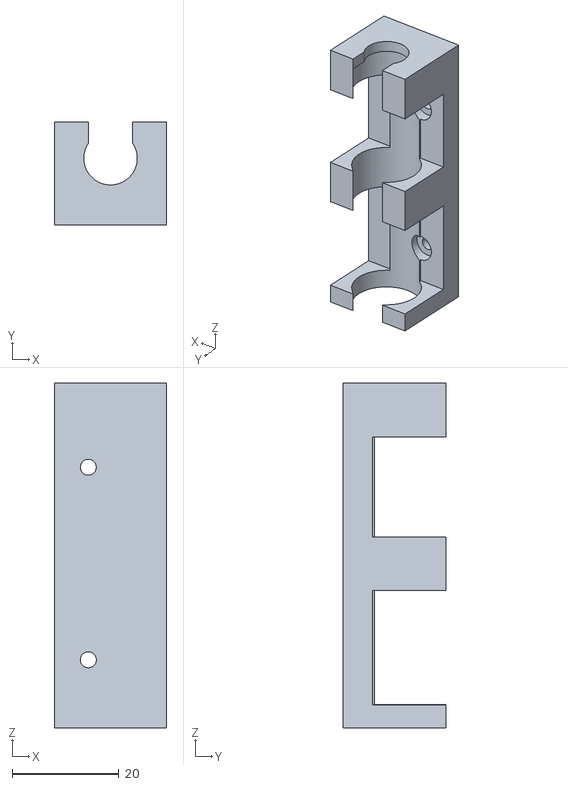
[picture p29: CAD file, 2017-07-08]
Images/QuadBot Iteration 6 (Update) (with colours)/1 x Battery Holder (ANY).stl
21.0 x 19.3 x 64.5

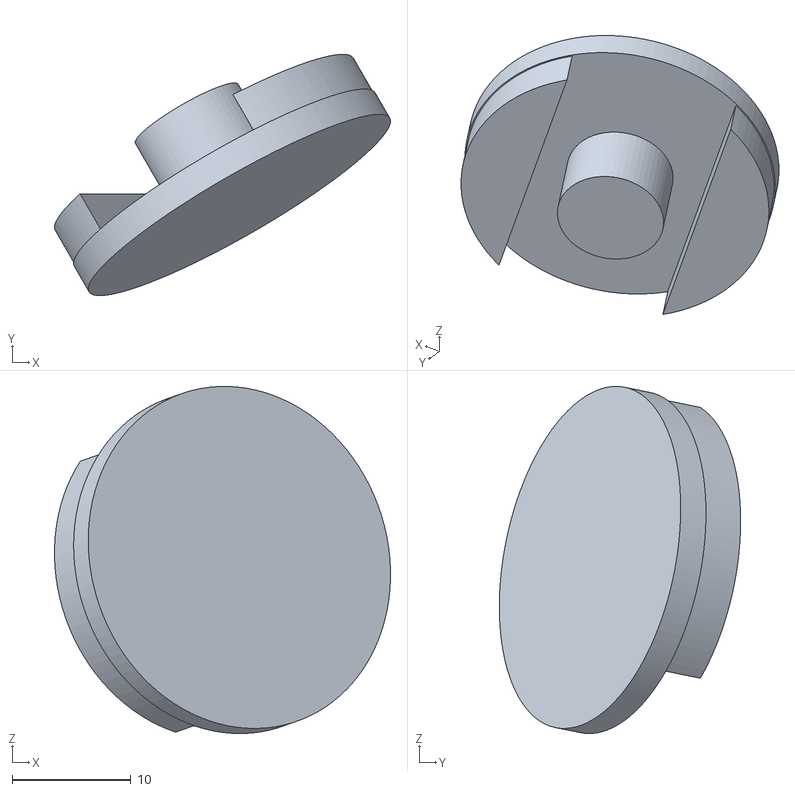
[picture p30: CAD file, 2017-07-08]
Images/QuadBot Iteration 6 (Update) (with colours)/2 x Eye Part 1 (BLACK).stl
28.3 x 20.3 x 29.2

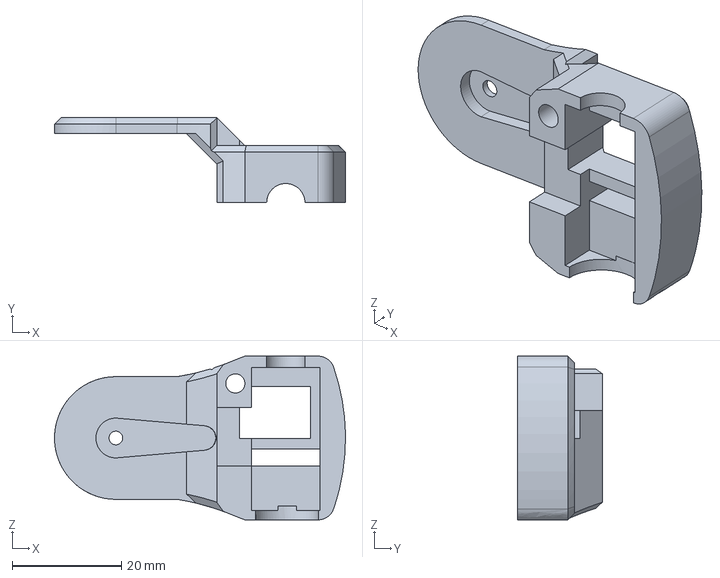
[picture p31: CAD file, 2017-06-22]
Mechanical/New Version/Components/Hip Servo (x4).iges
53.3 x 15.6 x 30.0 mm

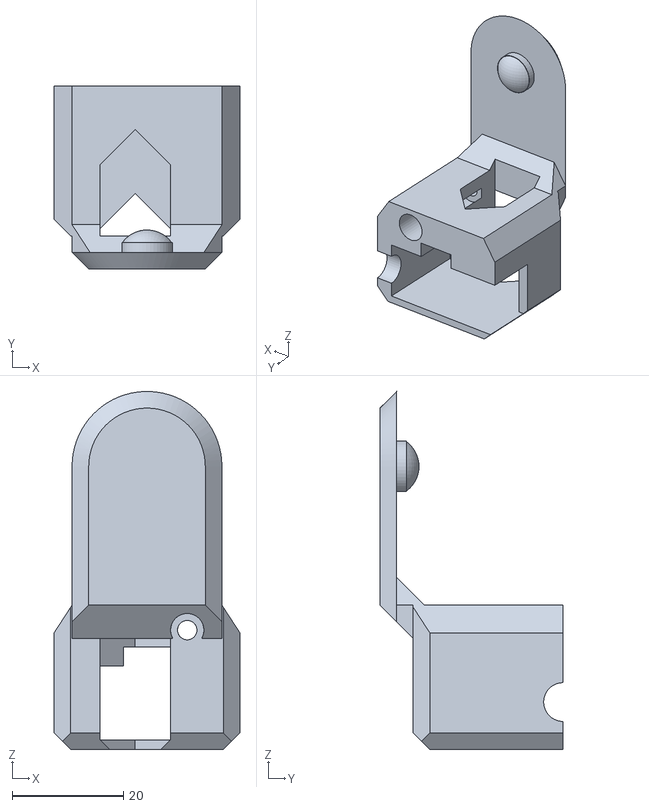
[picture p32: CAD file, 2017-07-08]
Images/QuadBot Iteration 6 (Update) (with colours)/4 x Hip Ball (WHITE).stl
33.5 x 33.0 x 64.5

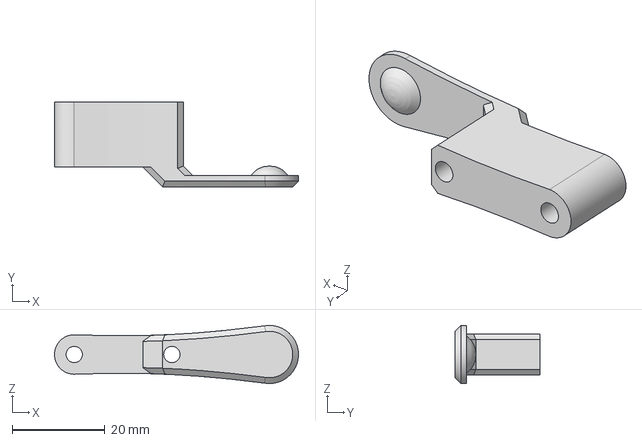
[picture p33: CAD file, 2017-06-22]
Mechanical/New Version/Components/Knee Ball (x4).iges
52.5 x 18.3 x 12.5 mm

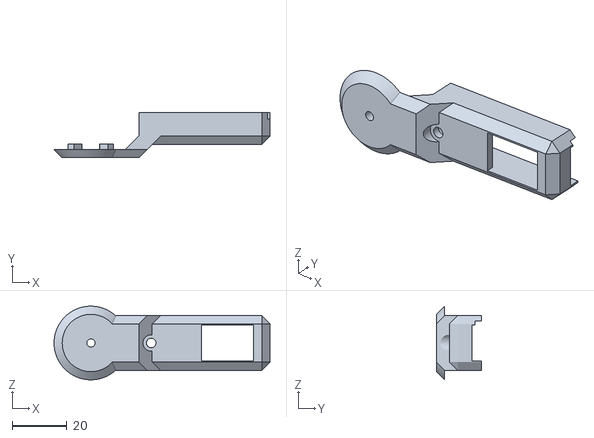
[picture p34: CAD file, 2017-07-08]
Images/QuadBot Iteration 6 (Update) (with colours)/4 x Knee Cross (BLACK).stl
79.1 x 16.6 x 27.0

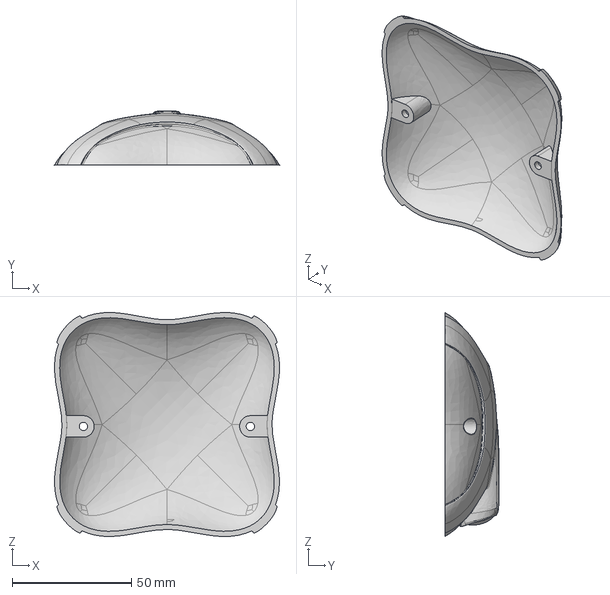
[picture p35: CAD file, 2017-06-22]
Mechanical/New Version/Components/Shell (x1).iges
94.4 x 22.8 x 94.0 mm

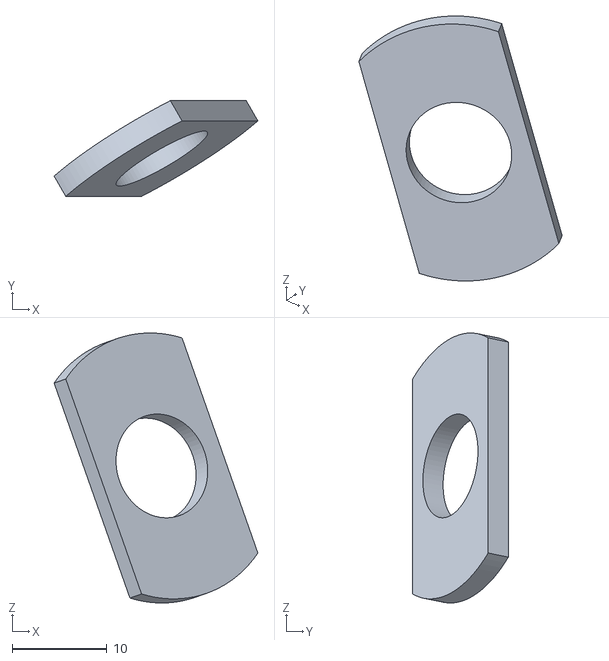
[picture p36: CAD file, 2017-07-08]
Images/QuadBot Iteration 6 (Update) (with colours)/2 x Eye Part 2 (WHITE).stl
21.5 x 10.1 x 28.5

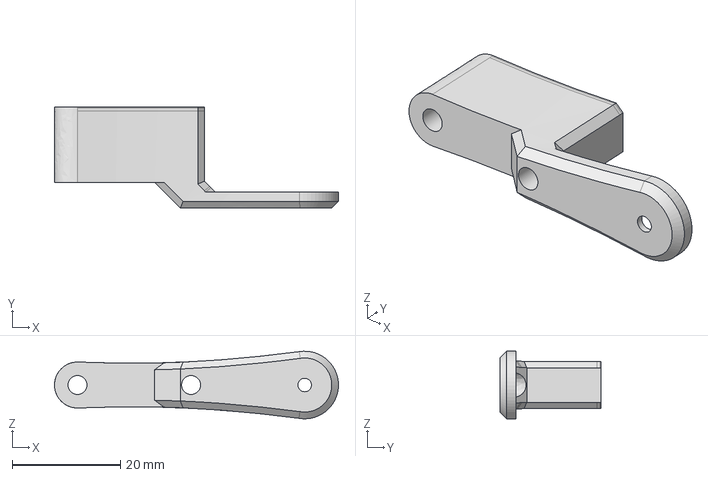
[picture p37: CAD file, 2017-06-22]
Mechanical/New Version/Components/Knee Servo (x4).iges
52.5 x 18.8 x 12.5 mm

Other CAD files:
Mechanical/New Version/Components/Link Flip (x8).iges
Mechanical/New Version/Components/Foot (x4).iges
Images/QuadBot Iteration 6 (Update) (with colours)/4 x Toe (BLACK).stl
Mechanical/New Version/Components/Shell Grip (x2).iges
Images/QuadBot Iteration 6 (Update) (with colours)/2 x Shell-Board Connector (WHITE).stl
Images/QuadBot Iteration 6 (Update) (with colours)/4 x Foot Ball (WHITE).stl
Images/QuadBot Iteration 6 (Update) (with colours)/4 x Foot Cross (WHITE).stl
Images/QuadBot Iteration 6 (Update) (with colours)/4 x Hip Cross (WHITE).stl
Mechanical/New Version/Components/Hip Servo (x4).f3d
Mechanical/New Version/Components/Knee Ball (x4).f3d
Mechanical/New Version/Components/Knee Servo (x4).f3d
Mechanical/New Version/Components/Link Flip (x8).f3d
Mechanical/New Version/Components/Pelvis (x4).f3d
Mechanical/New Version/Components/STLs/Hip Ball (x4).stl
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

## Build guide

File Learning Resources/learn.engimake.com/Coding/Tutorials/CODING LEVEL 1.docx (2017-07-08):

LEFT SIDEBAR | MAIN CONTENT
IMAGE
TITLE: CODING LEVEL 1
BLURB: Learn the very basics of computer coding.
LEFT MENU: ~What is Coding ~What are variables ~How do we use variables, ~What are functions ~What are structures, ~Conclusion

URL: engimake.com/coding/l1/0

What is Coding (H1)

Coding means telling a computer what to do. It’s how we make computers do what we want. Coding is like writing a set of instructions for someone to follow, except that the “someone” has no intelligence and needs to be told exactly what to do.

What’s the essence of what a computer can do?

The Five Ingredients of Coding (H2)

1) Input: Reading information from the outside world
2) Decisions: Making decisions based on information
3) Output: Sending information to the outside world
4) Math: Performing calculations
5) Repetition: Repeating operations many times

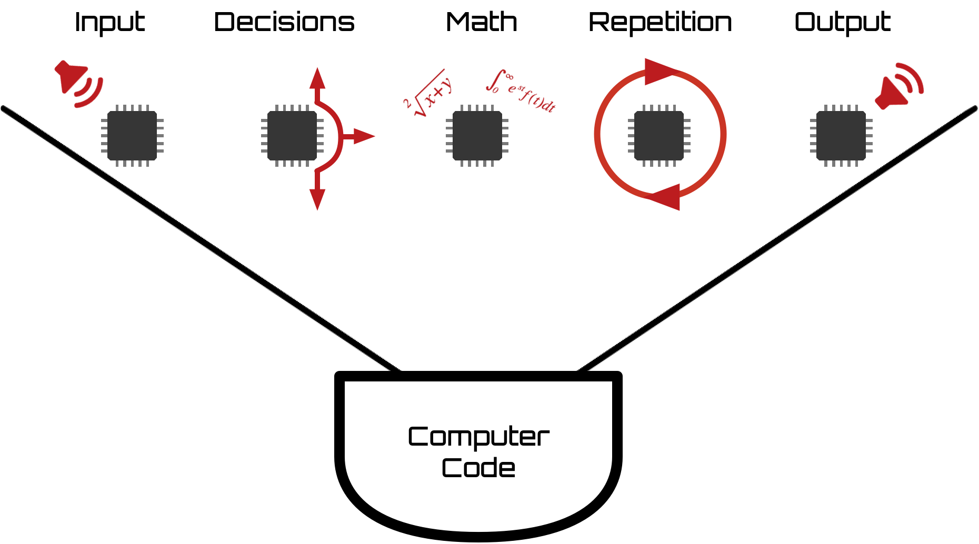
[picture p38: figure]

When we code, we mix these five ingredients together to create a program. Just how you might mix flour, milk, sugar and eggs to make a cake.

With the five basic ingredients, we have all the complexity of modern computers, smartphones, robots and so on. That’s it!

What does code look like? (H2)

There are many different types of code, each one is called a Programming Language. They are all different but share some characteristics.

1) Human Readable Syntax: Keywords and structure that a human can understand.
2) Data: Some way of handling data or information.
3) Operators and functions: Symbols or words that perform operations on data.
4) Comments: Text to document the code, that doesn’t affect the operation.

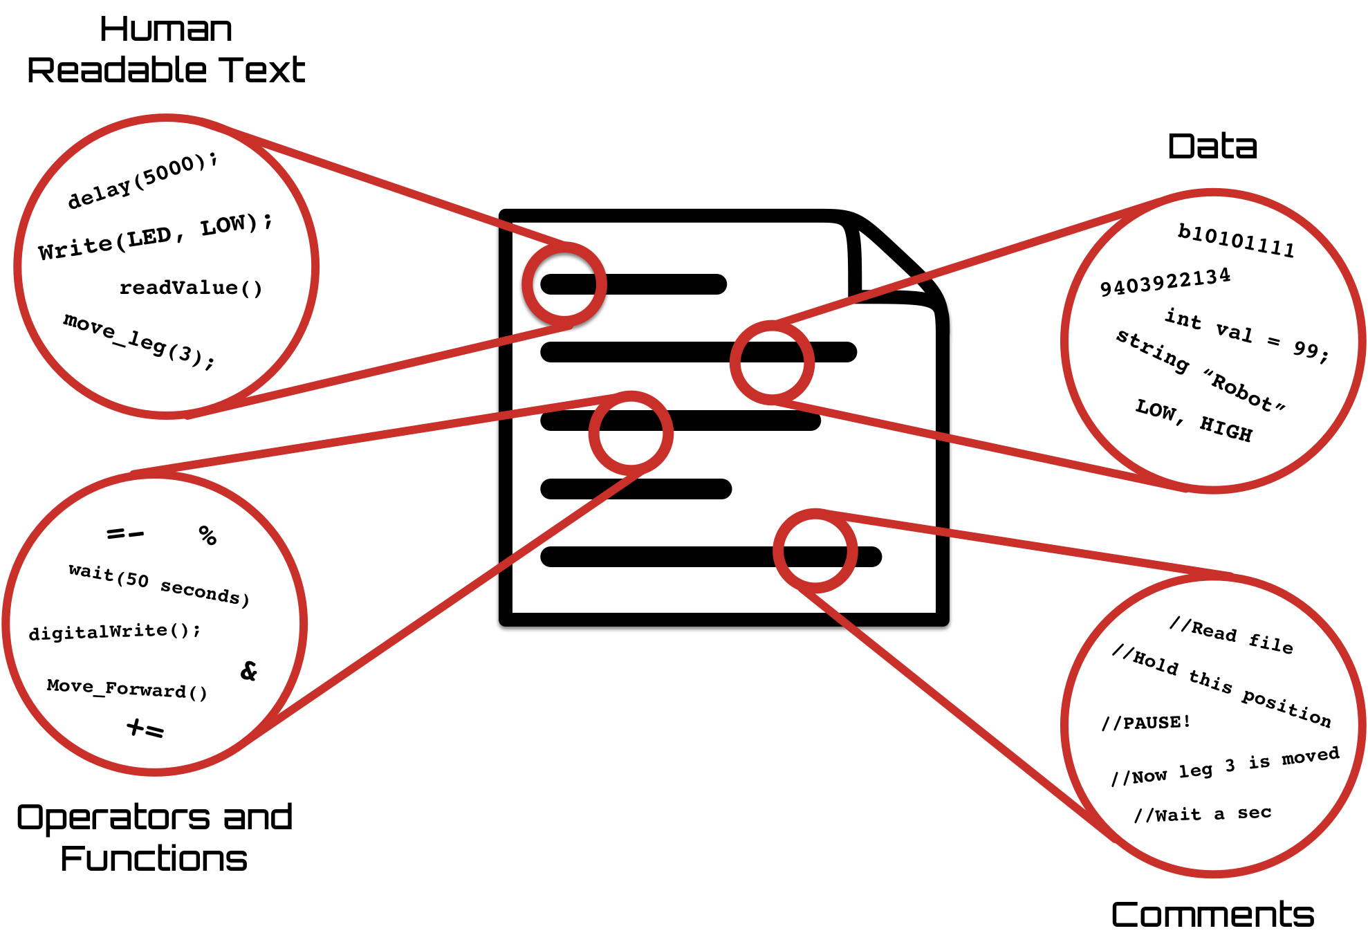
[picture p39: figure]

Here’s an example of some code…

while(1){ //Repeat forever

digitalWrite(13, HIGH); //Turn on LED on pin 13

delay(1500); //Program waits for 1.5 seconds

digitalWrite(13, LOW); //Turn off LED on pin 13

delay(1500); //Program waits for 1.5 seconds

}

This code uses some two different functions, some data, and a structure to flash an LED on an output pin of a computer. There are also comments to help a user understand to program.

Let’s dive into the details and look at the Arduino C++ language. This language is used to program Arduinos and QuadBot.

We use a semicolon ; to separate the code statements for each other
LEFT BUTTON NONE | RIGHT BUTTON TEXT: What are variables URL: engimake.com/coding/l1/1

URL: engimake.com/coding/l1/1

What are variables? (H1)

We use variables to store information in a program. A variable has a name, a type and a value.

- The type specifies what kind of information it is. For example a whole number, a character, a decimal number and so on.
- The value is the actual data we are storing.
- The name is what we use in a program to access the data.

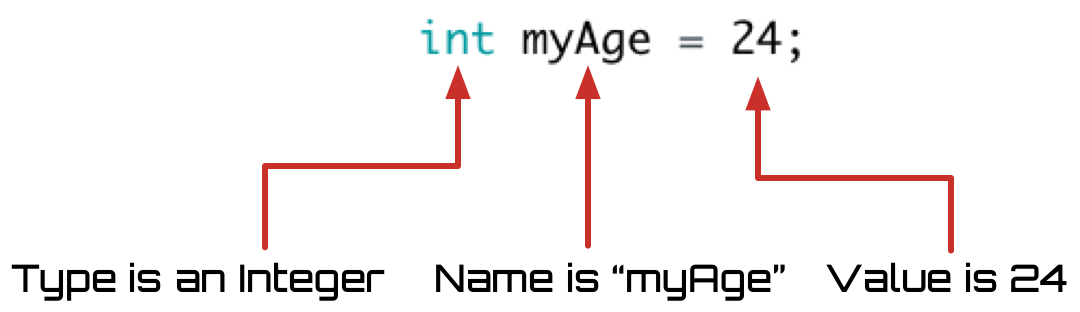
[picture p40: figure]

- This variable is an integer (whole number).
- The variable is called myAge.
- The value of the variable is 24.

Data Types (H2)

There’s loads of variable data types we can use depending on what we need. Here are some common ones we’ll use in the Arduino language.

Type | What does it store | Range | Example
byte | An integer | 0 to 255 | byte height = 181;
int | An integer | -2,147,483,648 to +2,147,483,647 | int time = 1700;
float | A floating point number (a number with a decimal point) | -3.4028235 x 10³⁸ to +3.4028235 x 10³⁸ | float weight = 76.2;
boolean | A single boolean number (1 or 0) | 1 or 0 | boolean hungry = 1;
char | A character, like a letter, symbol or number | All ASCII (https://www.arduino.cc/en/Reference/ASCIIchart) characters | char grade = ‘A’;
string | A string of characters | Any combination of characters | string name = “Josh”;

These are the data types you’ll see and use with QuadBot but there are many more data types (https://www.arduino.cc/en/Reference/HomePage).
LEFT BUTTON TEXT: What is coding URL: engimake.com/coding/l1/0 | RIGHT BUTTON TEXT: How do we use variables URL: engimake.com/coding/l1/2

URL: engimake.com/coding/l1/2

How do we use variables? (H1)

Declaration (H2)

First we must declare the variable to the computer. The computer can then allocate some memory to store that variable.

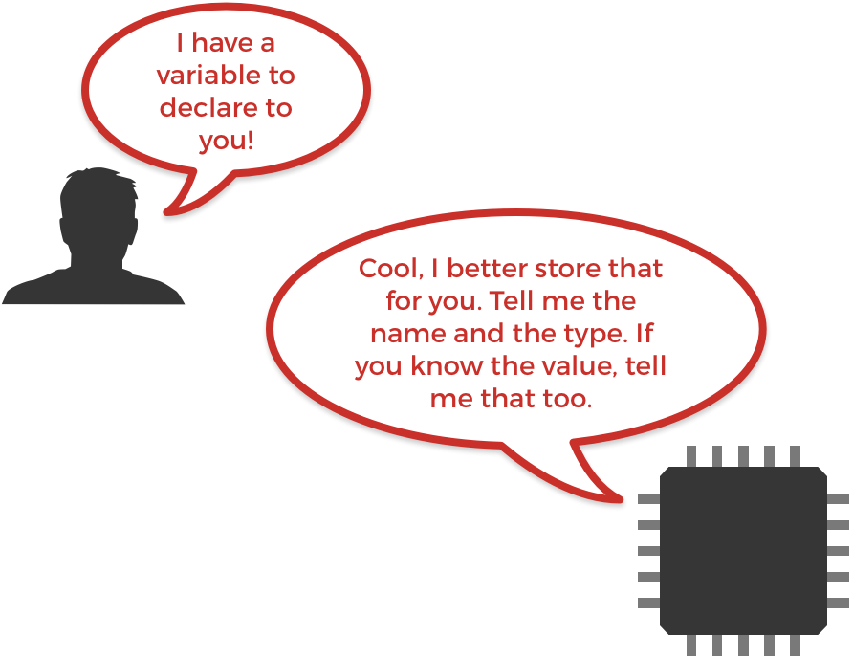
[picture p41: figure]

We must always tell the computer the name of the variable and the data type. We don’t have to tell the computer the value if we don’t know it yet.

int life;

Declares a variable called “life” of type int. We can now use the variable “life” in our program.

If we know the value, we can declare the value as well, like this…

int life = 42;

Declares a variable called “life” of type int, of value 42;

Remember! You must declare a variable before you can use it.

Writing (H2)

We can change the value of a variable by writing to it. The computer then stores the written value in the variable. We can do this as many times as we like.

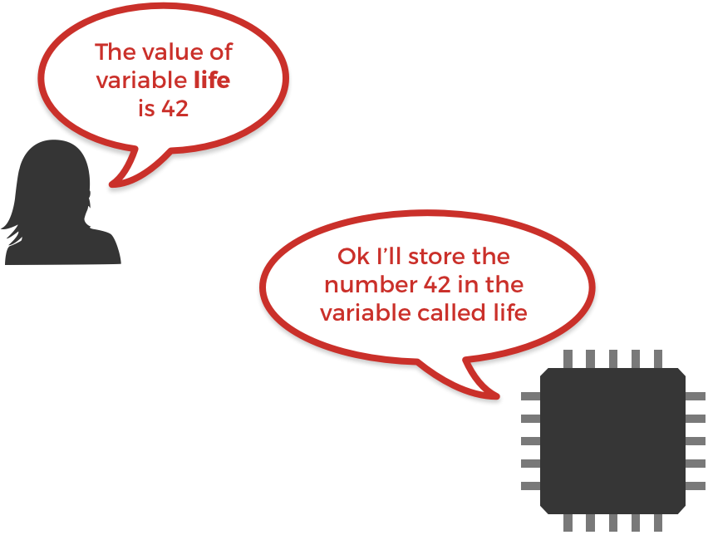
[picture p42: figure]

For example...

life = 42;

The value 42 is stored in life. If we then write...

life = 43;

Now the value is 43. The previous value of 42 is lost. If we write...

life = 41 + 1;

life now has a value of 42 again.

Remember! A variable can only store a variable with the matching data type. For example an int cannot store a char!

Reading (H2)

We can access the value of a variable by reading it.

We read the value of a variable in our program. Reading a variable is simple, you just call it’s name.

life;

The computer reads the value of the variable, but it hasn’t actually done anything with useful with that variable. A better idea is to read that variable inside a function like this...

print(life);

The computer reads the value of life and then prints it for the user to see. We could also read the value of life and use it to initialize a different variable.

int universe = life;

The value of life is written to the integer called universe.

That’s the basics of how computer programs store data. Let’s move on to functions…
RIGHT BUTTON TEXT: What are variables URL: engimake.com/coding/l1/1 | LEFT BUTTON TEXT: What are functions URL: engimake.com/coding/l1/3

URL: engimake.com/coding/l1/3

What are Functions? (H1)

Functions do the heavy work in programs. They do the calculations, the input and output, and just about everything else. The print() statement we just explored was a function...

print(life);

Functions can accept data as inputs and return data as an output. Some functions don’t accept or return any data. Others only either accept or return data. For our print function…

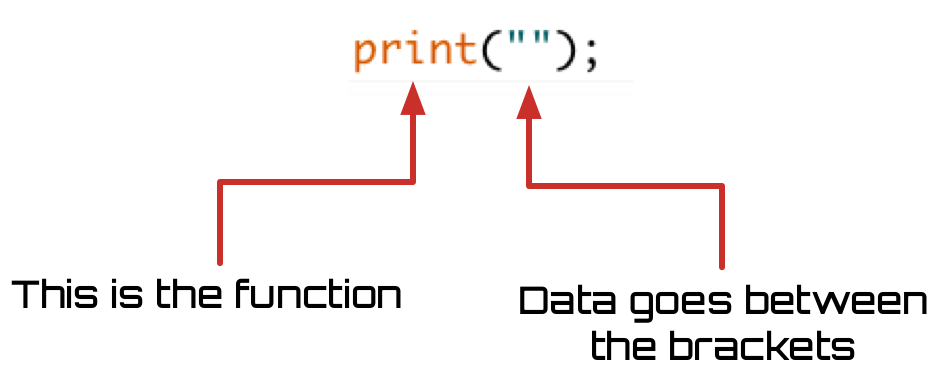
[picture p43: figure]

The delay function is another common one we’ll use.

delay(5000);

This function tells the computer to wait for 5 seconds. It takes the delay time as an input, and does not return anything.

There are many functions we’ll use for QuadBot, but you won’t have to memorize them. You can find out how to use each one on the Arduino reference page (https://www.arduino.cc/en/Reference/HomePage) and our QuadBot reference page.
RIGHT BUTTON TEXT: What are variables URL: engimake.com/coding/l1/1 | LEFT BUTTON TEXT: What are Structures URL: engimake.com/coding/l1/3

dsadasd

URL: engimake.com/coding/l1/3

What are Structures? (H1)

How do programs run? It’s all in the structure…

The programs we’ll be writing are sequential; operations happen one after the other, from left to right, top to bottom.

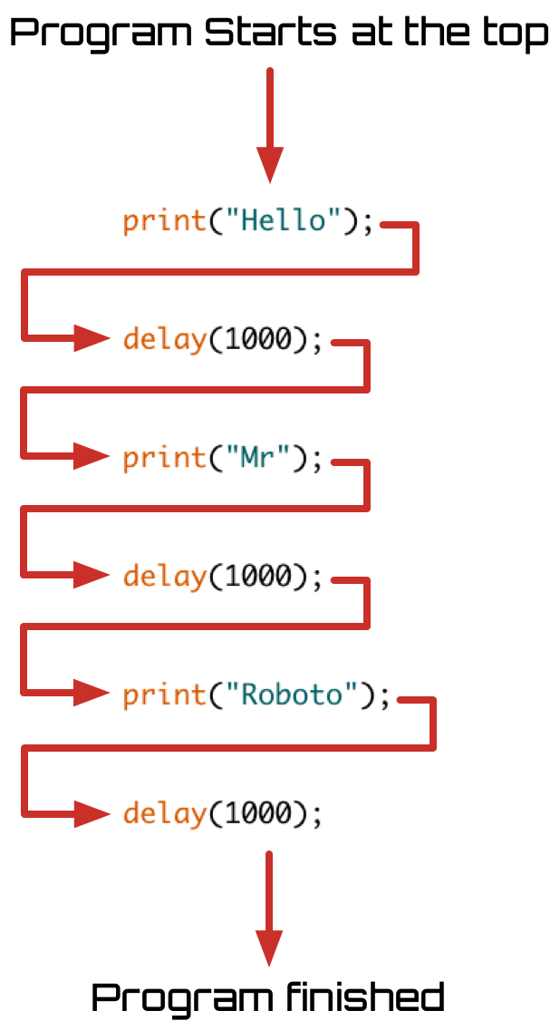
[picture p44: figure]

This program starts at the top and runs through the functions one at a time. Believe it or not, we could write the same program like this…

Remember! White spaces do not make an difference in C++. You could write all your code on a single line if you wanted to.

A good coder will always add spaces in their code to make it easy for others to read.

Loops and how to use them (H2)

In most programs we’ll want a computer to repeat itself over and over again. If we wanted the computer to print “Robots are awesome!” continuously, we could do so like this…

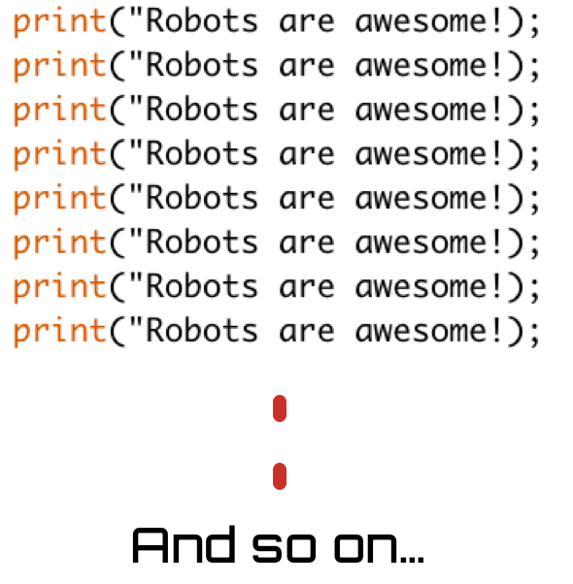
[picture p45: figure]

But this the slow way, a better way is to use a repeating loop.

While loop (H2)

A while loop is a structure that repeats any statements inside it while a condition is true.

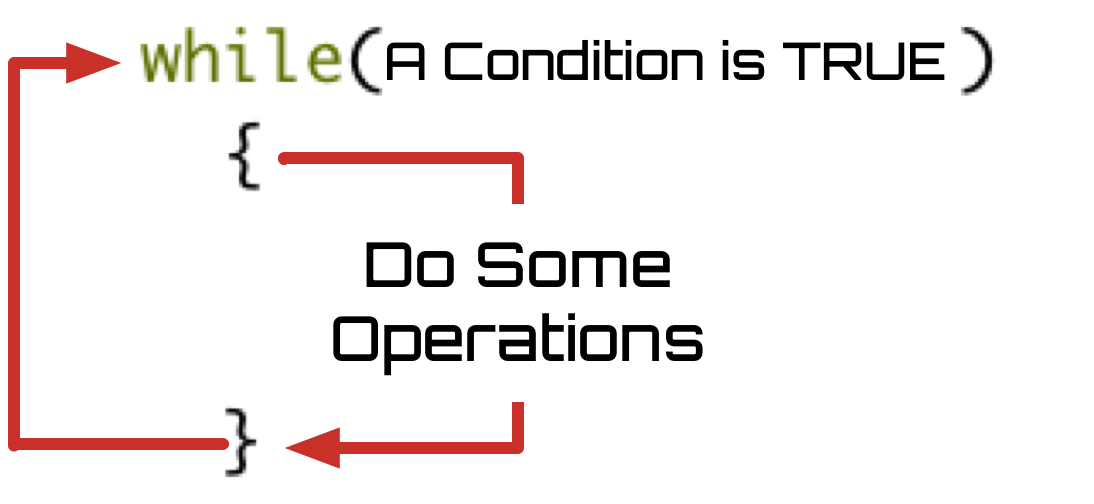
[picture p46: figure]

For example…

while(loopCount < 10){ //Repeat this code while loopCount < 10

print(“Robots are awesome!”); //Print the text to the user

}

This code will keep printing “Robots are awesome!” until the variable loopCount becomes more than 10. The problem is, nothing is going to make loopCount increase, so it will never be more than 10. That means the loop will never stop.

We can fix this by initializing loopCount to 0 before the loop, and adding 1 to loopCount every time the loop runs.

int loopCount = 0; //Initialize loopCount to 0

while(loopCount < 10){ //Repeat this code while loopCount < 10

print(“Robots are awesome!”); //Print the text to the user

loopCount = loopCount + 1; //Add 1 to the value of loopCount

}

After the tenth pass of the loop, loopCount is 10 so the loop stops running. You’d see “Robots are awesome” printed 10 times.

For loop

If we know for sure how many times we want a loop to run, for example in math calculations, we can use a For loop.

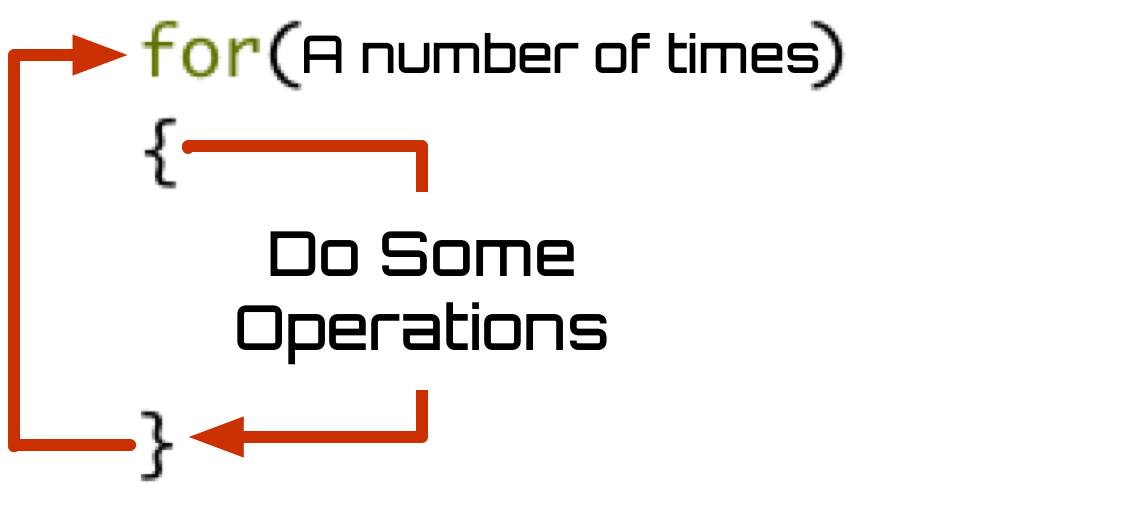
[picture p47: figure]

Here’s what that actually looks like.

for(int i=0 ; i<0 ; i=i+1){

Serial.println(“Still awesome”);

}

To control the loop, we use the code inside the for() brackets.

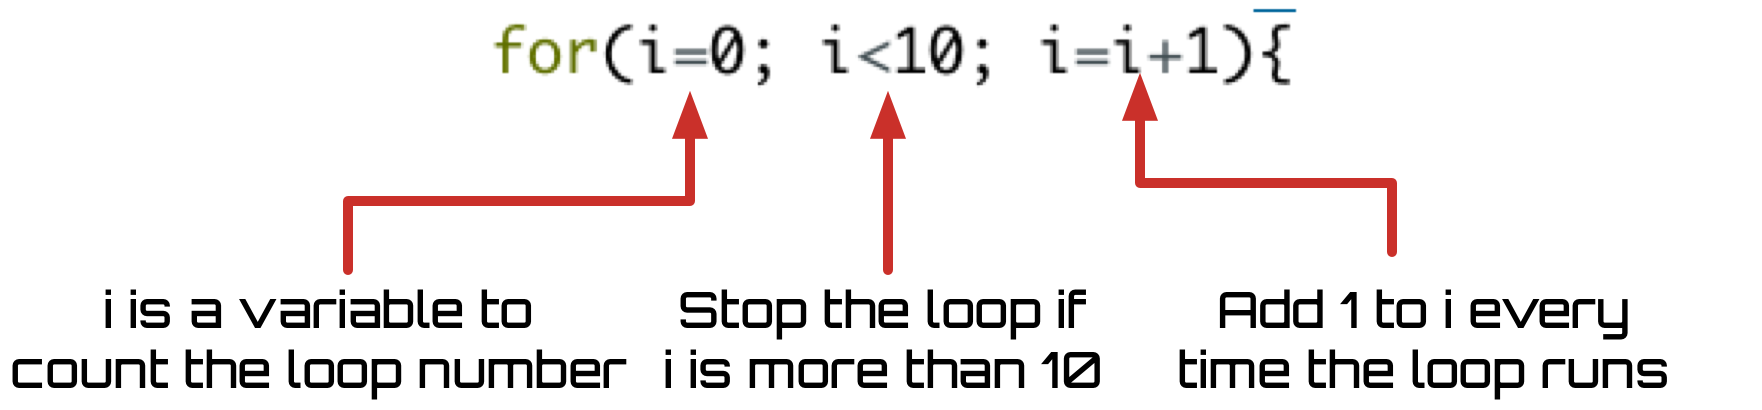
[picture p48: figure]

i starts at 0 and increments every time the loop runs. When i is more than 10, the loop stops.

Like the while loop, this code will print “Still awesome” 10 times!

If-else statement (H2)

If-else are structures to make decisions in code. Based on whether a condition is true or false, a different piece of code will run.

Remember! True and false are the two boolean values we can use.

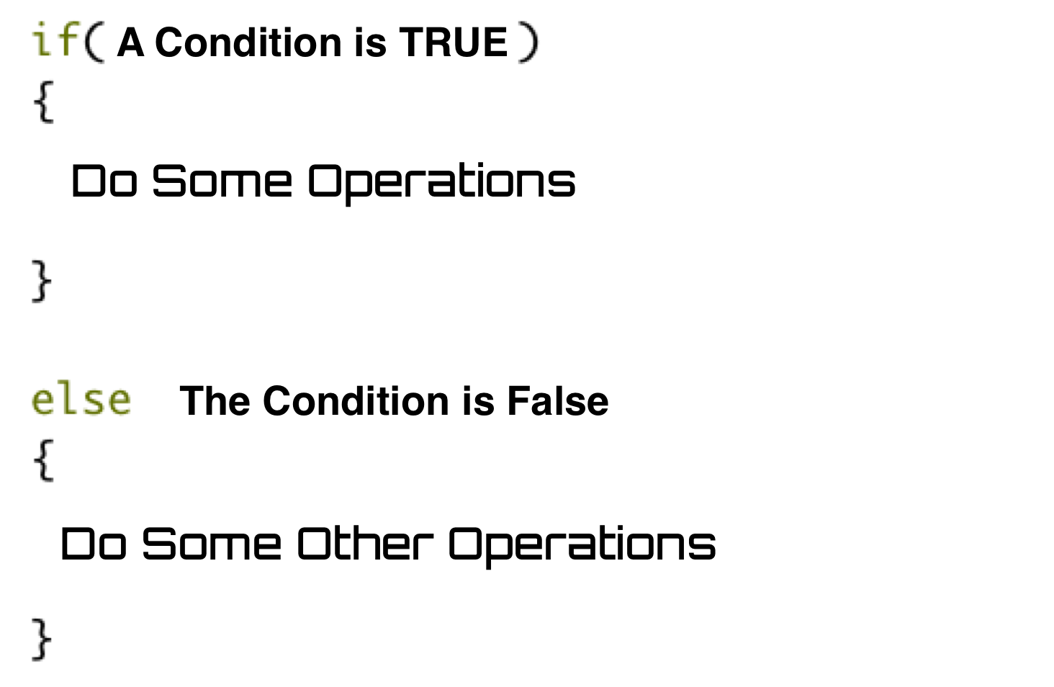
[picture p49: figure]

For example…

if(robots > 10){

println(“Awesome, over 10 robots”);

}

else{

println(“Sad times”);

}
RIGHT BUTTON TEXT: What is coding URL: engimake.com/coding/l1/2 | LEFT BUTTON TEXT: Wrap up URL: engimake.com/coding/l1/4

URL: engimake.com/coding/l1/4

Conclusion (H1)

You should now be armed with the knowledge you need to understand basic programming…

Now move on to input and output...
RIGHT BUTTON TEXT: NONE | LEFT BUTTON TEXT: Input and Output URL: engimake.com/coding/io1/0

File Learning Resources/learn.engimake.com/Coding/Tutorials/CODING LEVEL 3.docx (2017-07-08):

LEFT SIDEBAR | MAIN CONTENT
IMAGE
TITLE: CODING LEVEL 3
BLURB: Get the final coding knowledge you’ll need to program QuadBot
LEFT MENU: Functions, Writing Functions

URL: engimake.com/coding/l3/0

Functions (H1)

A function is a group of statements that perform a task. They are the building blocks of any program, performing the computations, decisions and IO.

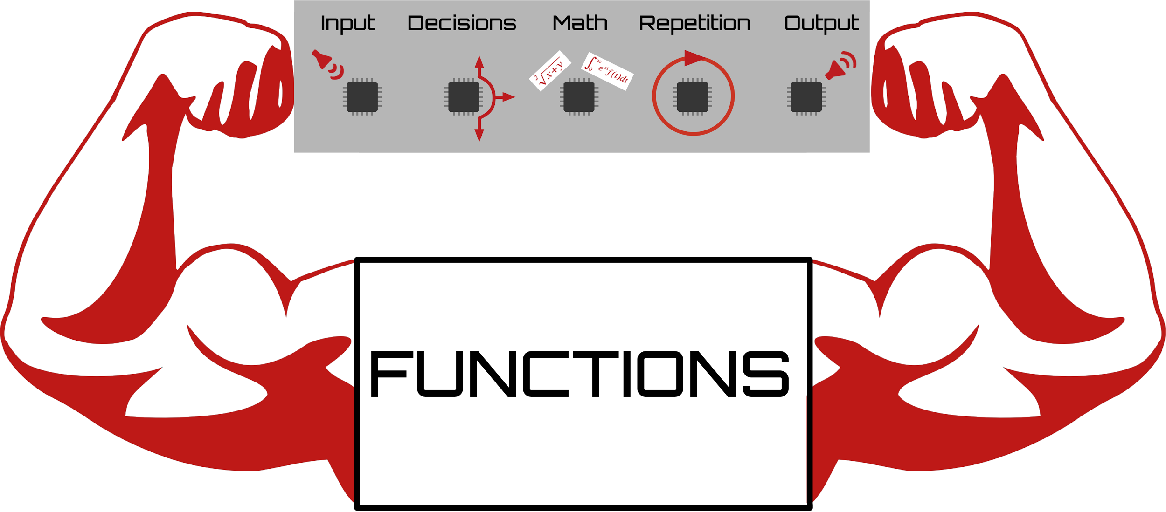
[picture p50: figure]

Inputs (H2)

Functions take input parameters if they need to work with data. Most, but not all functions do need to take input data. It really depends on what the function does. The function below is called digitalWrite, and it takes two inputs, pin number and state.

digitalWrite(3, LOW);

This function will write a value of LOW (0 volts) to digital pin number 3.

Functions expect you to give them the right type of data. For example if you tried to write the statement below…

digitalWrite(‘A’, LOW);

There’s no digital pin called ‘A’, so this code wouldn’t work.

Outputs

Some functions return data after they have run. Math functions tend to do this because they have to return a result.

Value = sin(1.2);

The sin function returns the calculated value, which is stored in the variable named value.

Remember! For functions that return data, you need to store that data in a variable. Simply calling the function without storing the data means the data will be lost.
| LEFT BUTTON TEXT: Writing Functions URL: engimake.com/coding/l3/1

URL: engimake.com/coding/l3/1

Writing Functions (H1)

All the functions we’ve used so far come with the Arduino environment, but it’s very useful to be able to write our own functions.

To do this we must first define the function prototype, this defines the name of the function, the inputs and the output.

To do this we must first define the function prototype, this defines the name of the function, the inputs and the output.

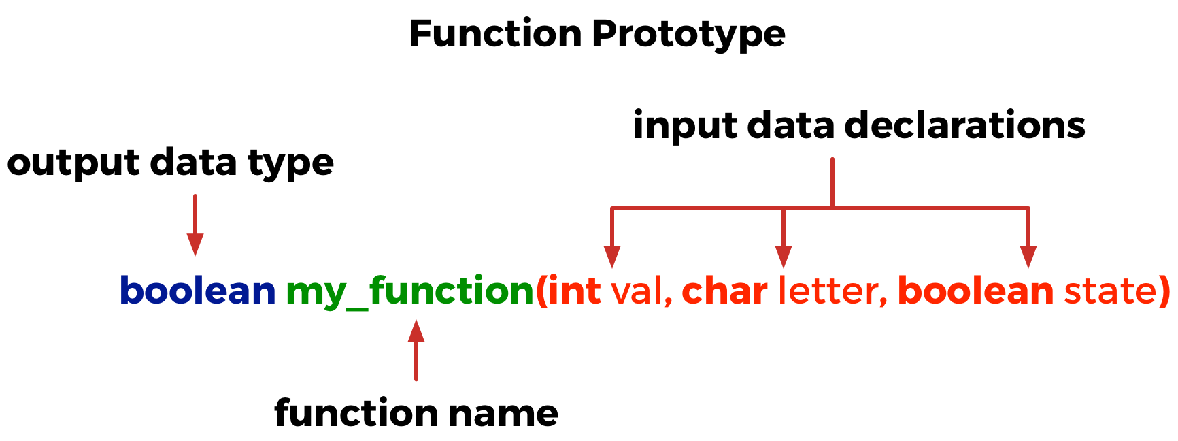
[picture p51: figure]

Defines a function called “my_function”, that takes three inputs; an integer called val, a character called letter and a boolean called state. The function outputs a boolean type.

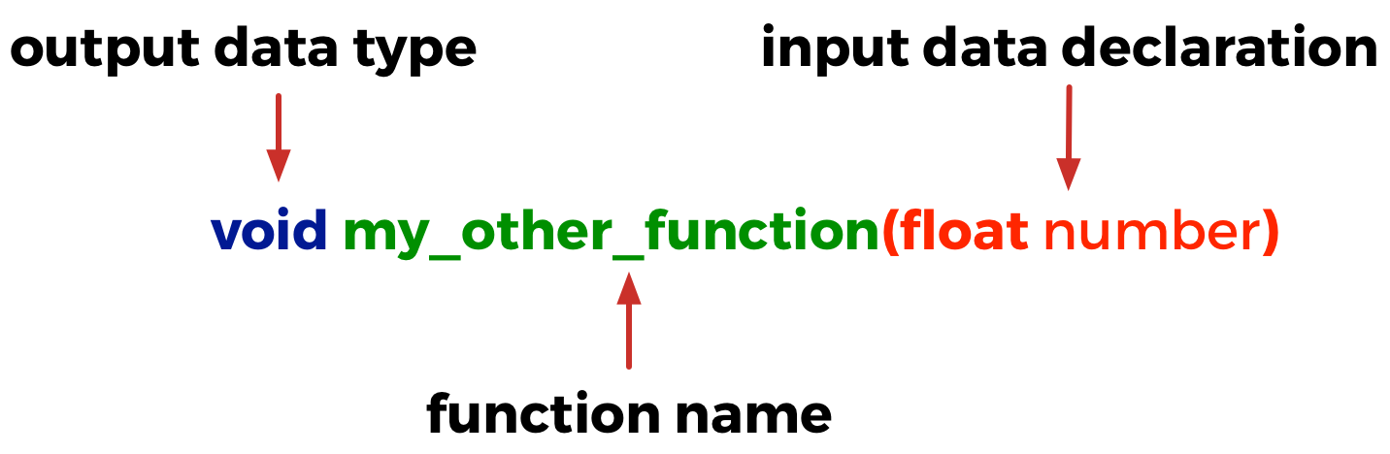
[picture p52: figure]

This defines a function called “my_other_function” that takes a float type input. The “void” return type means the function doesn’t return anything.

After the function prototype we must write the operations that make up the function. Let’s take our example of a flashing LED from the previous example and write a function for it.

Here is the initial code using only the Arduino functions

int outputPin = 3;

int delayTime = 1000;

void setup(){

pinMode(outputPin, OUTPUT);

}

void loop(){

digitalWrite(outputPin, LOW);

delay(delayTime);

digitalWrite(outputPin, HIGH);

delay(delayTime);

}

Let’s write our own function for the code that flashes the LED.

void flash(int pinNumber){

digitalWrite(outputPin, LOW);

delay(1000);

digitalWrite(outputPin, HIGH);

delay(1000);

}

Now we can rewrite our code like this…

int outputPin = 3;

int delayTime = 1000;

void setup(){

pinMode(outputPin, OUTPUT);

}

void loop(){

flash(3);

}

void flash(int pinNumber){

digitalWrite(outputPin, LOW);

delay(1000);

digitalWrite(outputPin, HIGH);

delay(1000);

}

Look how simple the code inside loop() has become. This is one benefit of functions, it makes our code a lot easier to read and understand. We could even place the function definition in a separate file and keep our main program even cleaner!

You might notice now that loop() and setup() are both functions that take no input data and output no data!
RIGHT BUTTON TEXT: What is coding URL: engimake.com/coding/l3/0 | LEFT BUTTON TEXT: Conclusion URL: engimake.com/coding/l3/2

URL: engimake.com/coding/l3/2

Conclusion (H1)

Great job! You’re now clued up on coding and will be able to understand the basic structure of code that we’ll write for QuadBot. Now try the input and output tutorials.

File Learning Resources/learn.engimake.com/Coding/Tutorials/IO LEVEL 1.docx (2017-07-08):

LEFT SIDEBAR | MAIN CONTENT
IMAGE
TITLE: CODING LEVEL 1
BLURB: Learn the very basics of computer coding.
LEFT MENU: Input and output Signal types Hardware overview Digital input/output Analog input Conclusion

URL: engimake.com/coding/io1/0

Input and output (H1)

Any robot must be interact with the outside world. That means the robot’s computer must be able to input and output information.

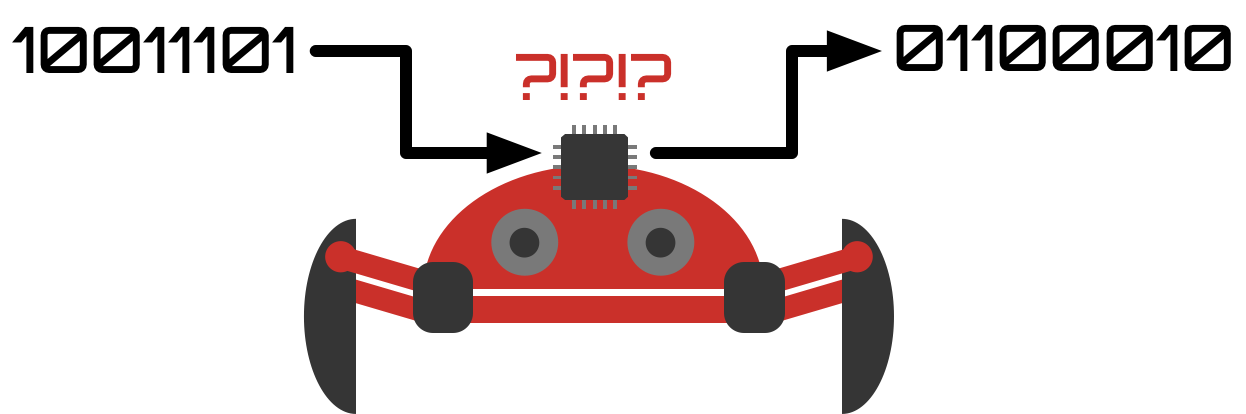
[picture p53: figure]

QuadBot uses a special type of computer called a microcontroller. A microcontroller isn’t as powerful as the computers in the device you’re reading this on, but it has some very useful features...

1) Input and Output: Microcontrollers have built-in features to make input and output easy.
2) Lots of pins: Microcontrollers have a lot of pins for input and output.
3) Memory: Microcontrollers have built-in memory to store programs and data.
4) Single thread: Microcontrollers only runs one program at a time.
5) Embedded: Microcontrollers love to be embedded into larger systems, like robots.
6) Low power: Microcontroller are low power, perfect for battery powered robots.
7) Rugged: Microcontrollers are quite tolerant of voltages and electrical noise.

Let’s look at different types of signals…
RIGHT BUTTON TEXT URL | LEFT BUTTON TEXT: Signal Types URL: engimake.com/coding/l1/1

URL: engimake.com/coding/l1/1

Signal Types (H1)

Signals can be divided into one of two different types, digital and analog.

Digital Signals (H2)

Digital Signals can be in only one of two states. On or Off. High or Low. True or False. Jekyll or Hyde (you get the idea).

Physically this means either a high voltage or a low voltage. For QuadBot, a High signal means 5 volts on a wire, whereas a low one means 0 volts on a wire.

This is how all computers work with information. Digital data is stored as voltages, either High or Low inside the computer. It’s a Boolean digIT so we call it a BIT.

Remember! A digital signal can only be either 0 Volts or 5 Volts. Any voltage in between will not be understood by QuadBot

Analog Signals (H2)

Analog signals are the opposite of digital signals. They can be any voltage between 0 and 5 volts. Analog is how the real world works. For example the loudness of your voice isn’t just two values. If you used a microphone to convert this sound into a voltage, you’d see the voltage vary continuously between 0 volts and 5 volts.

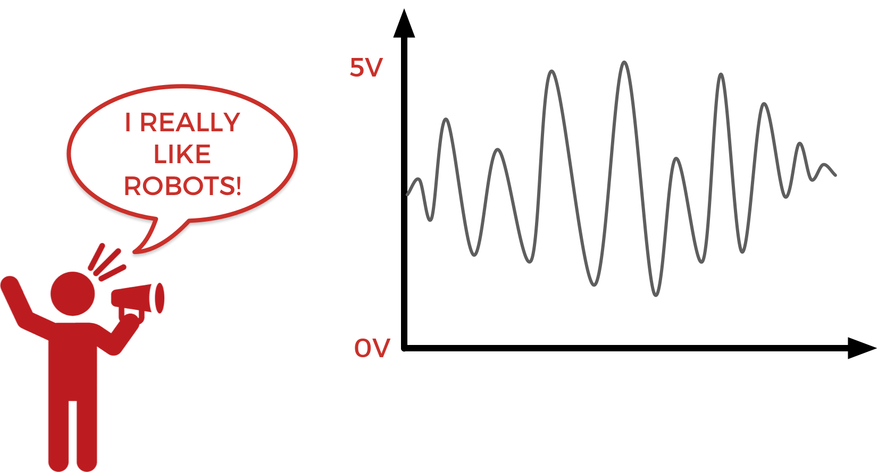
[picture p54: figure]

Microcontrollers are digital beasts so how can they understand an analog signal like that? Well, they use a little device called an analog to digital converter (ADC) to read this data, and convert it into a digital value. Since microcontrollers are so awesome, these ADCs are built-in!

Now let’s look into the microcontroller on QuadBot to understand the input and output capabilities we have.

Remember! Analog signals can vary continuously between two voltages.
RIGHT BUTTON TEXT: Input and output URL: URL: engimake.com/coding/l1/0 | LEFT BUTTON TEXT: Hardware overview URL: URL: engimake.com/coding/l1/2

URL: engimake.com/coding/l1/2

Hardware overview (H1)

The microcontroller (H2)

The microcontroller on QuadBot is called the atMEGA32u4.. Catchy right? It looks like this...

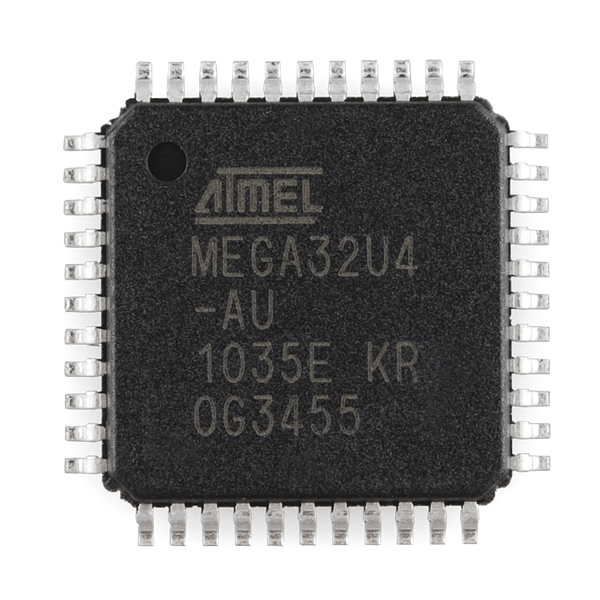
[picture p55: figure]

It’s a black box with 44 metal pins. These pins allow it to communicate with the outside world, so let’s see what they do.

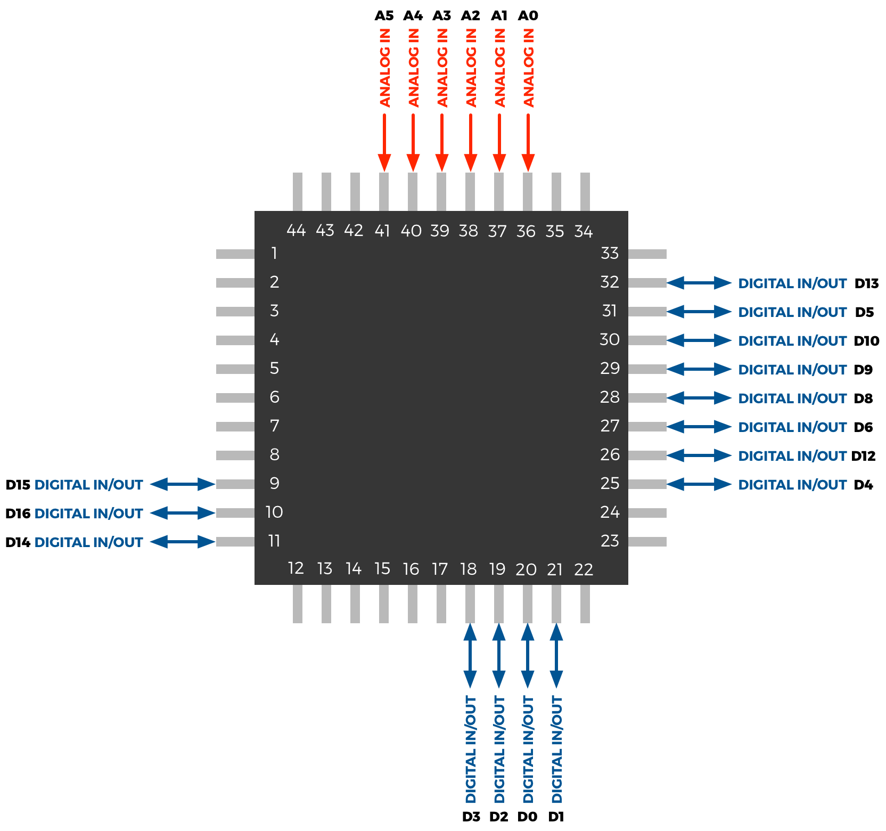
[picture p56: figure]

There’s 21 pins being used in total. The remaining pins do other functions that we won’t worry about in this tutorial (more on this later). There are two types.
RIGHT BUTTON TEXT: Signal Types URL: engimake.com/coding/l1/1 | LEFT BUTTON TEXT: Digital Input/Output URL: engimake.com/coding/l1/3

URL: engimake.com/coding/l1/3

Digital Input/Output (H1)

These are pins that the microcontroller can use to read digital signals from. Remember that digital signals can be in one of two states, so if we connected a switch to a digital input/output pin like this…

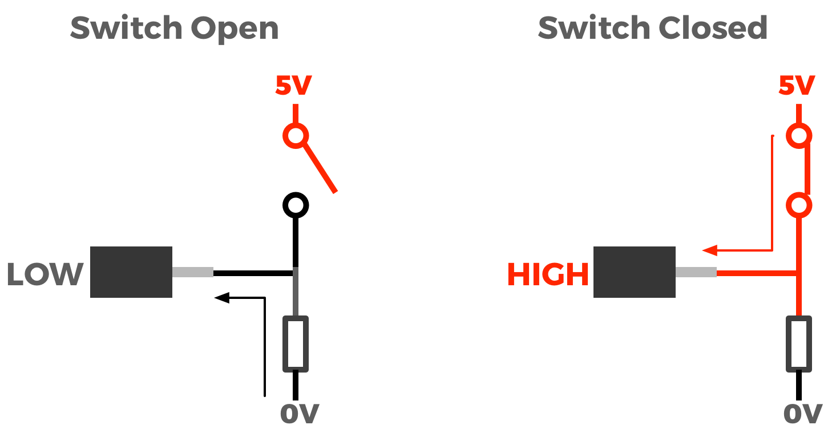
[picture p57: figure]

When the switch is open, we’d read LOW on this pin. When the switch is closed, we’d read HIGH on this pin.

Digital pins are special because they can also be used as either inputs or outputs. We have to choose whether we’d like a pin to be an input or an output in our program like this...

pinMode(PIN, INPUT); //Sets PIN as an input

pinMode(PIN, OUTPUT); //Sets PIN as an output

In the same program we can change a pin from an input to an output, but it cannot be an input and an output at the same time.

Let’s put an LED on a digital pin and see what happens.

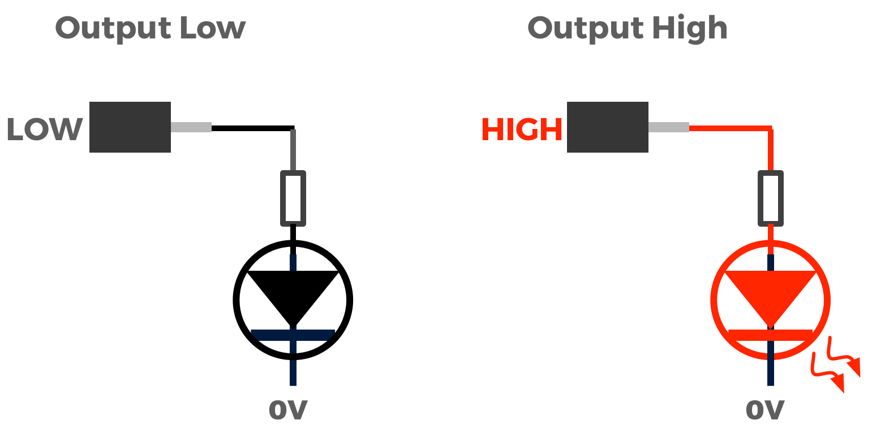
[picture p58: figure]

We can set the output like this.

digitalWrite(PIN, HIGH); //We set PIN to HIGH, turning on the LED

digitalWrite(PIN,LOW); //We set PIN to LOW, turning off the LED
RIGHT BUTTON TEXT: Hardware Overview URL: engimake.com/coding/l1/2 | LEFT BUTTON TEXT: Analog Input URL: engimake.com/coding/l1/4

URL: engimake.com/coding/l1/4

Analog Input (H1)

Our microcontroller has six pins that can be used for analog input. Unlike the digital pins, these analog pins can only be used for input, they cannot output an analog voltage. So how does it work?

Let’s look at the following circuit...

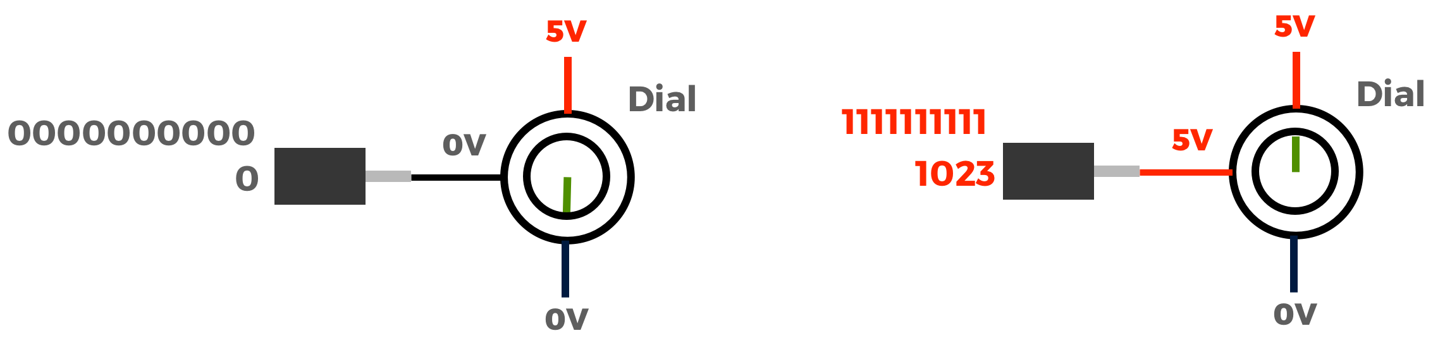
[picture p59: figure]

We’ve connected a dial to an analog pin. That dial outputs a voltage between 0 and 5 volts into the analog pin.

When the dial is in the lowest position, 0V is at the analog pin of the microcontroller. What happens now?

The microcontroller reads this voltage as a number between 0 and 1023. 0 means 0V, whereas 1023 means 5V. Why does the microcontroller use the number 1023 as the maximum?

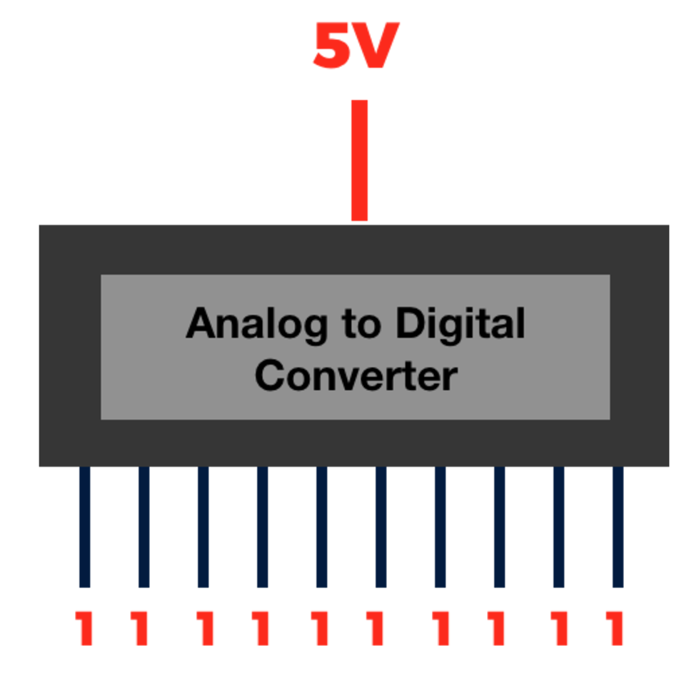
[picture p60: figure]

The microcontroller uses 10 binary digits (Bits) to store the voltage value, and since the largest number that can be stored in 10 bits is 1023, this represents the maximum voltage. What happens when the dial is in the middle position...

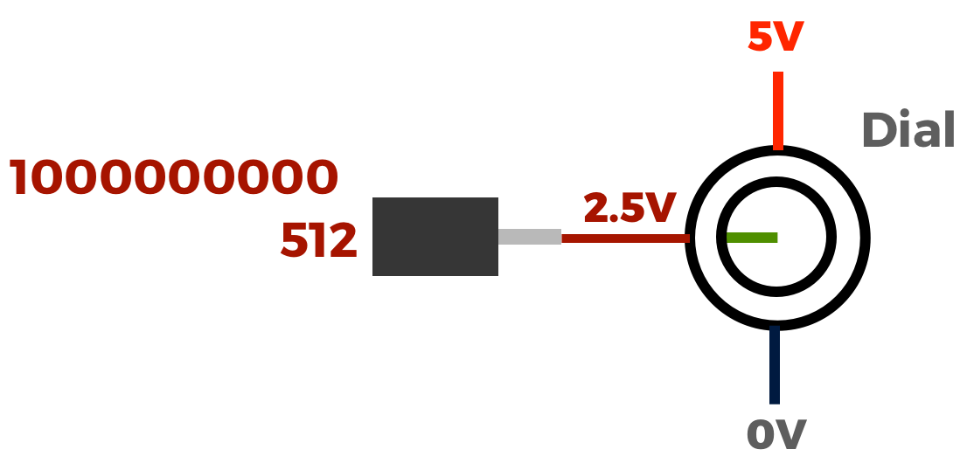
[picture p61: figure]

2.5 volts is read by the microcontroller as the value of 512 (1000000000 in binary), since 512 is 1023 divided by 2 (rounded up).
RIGHT BUTTON TEXT: Digital Input/Output URL: engimake.com/coding/l1/3 | LEFT BUTTON TEXT: Conclusion URL: engimake.com/coding/l1/5

URL: engimake.com/coding/l1/5

Conclusion

Great job! That’s your first taster of input and output, and is enough to get you going on simple programs for QuadBot. For more advanced programs, move on to the second tutorial for input and output.
RIGHT BUTTON TEXT URL | LEFT BUTTON TEXT URL

URL: engimake.com/coding/l1/0

What is Coding (H1)

Coding means telling a computer what to do. It’s how we make computers do what we wa
RIGHT BUTTON TEXT URL | LEFT BUTTON TEXT URL

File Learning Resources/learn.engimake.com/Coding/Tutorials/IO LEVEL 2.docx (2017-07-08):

LEFT SIDEBAR | MAIN CONTENT
IMAGE
TITLE: CODING LEVEL 1
BLURB: Learn the very basics of computer coding.
LEFT MENU: Overview, Pulse Width Modulation, Servo Comms, Serial Comms, Conclusion

URL: engimake.com/coding/l1/0

Overview (H1)

Microcontrollers would be quite limited if digital IO and analog input were the only capabilities. In reality there’s a whole lot more IO capabilities microcontrollers can achieve…

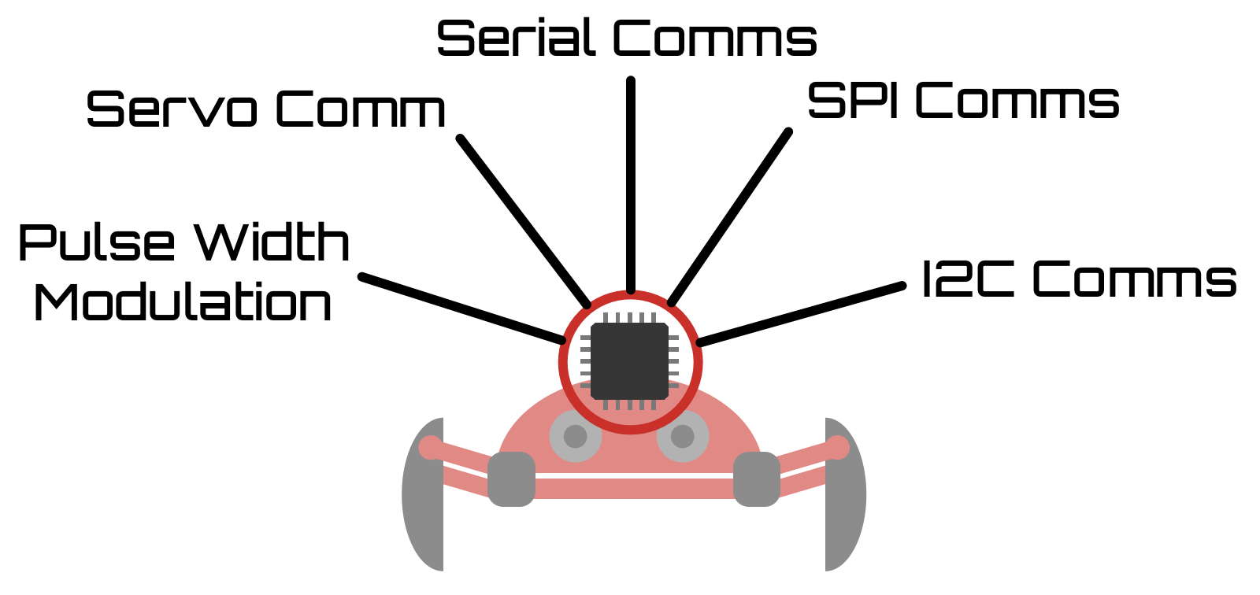
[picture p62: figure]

Let’s explore some of these...
RIGHT BUTTON TEXT URL | LEFT BUTTON TEXT: Pulse Width Modulation URL: engimake.com/coding/l1/1

URL: engimake.com/coding/l1/1

Pulse Width Modulation (H1)

Pulse width modulation (PWM) is a method used to send analog data from a digital output. This seems impossible since a digital output can only either be 0V or 5V.

The trick is that we can vary the time that the signal is at 5V, like a pulse. By varying the time that the pulse of the, we can, send out an analog signal. However it’s not the voltage that is analog, but the pulse width. We modulate the pulse width to send analog information.

We can start with a signal that has the same time duration for 5V and 0V.

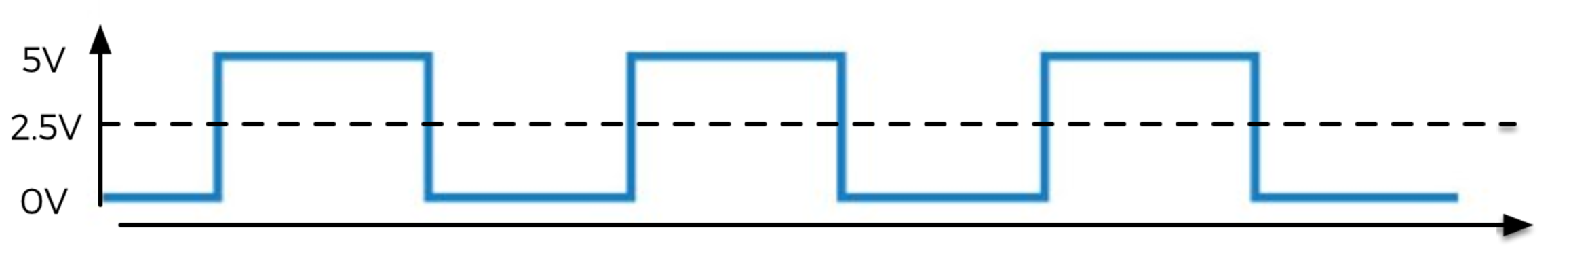
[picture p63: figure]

We call this a PWM signal with 50% duty cycle, because the signal is 5V for 50% of the time. The average of this signal is 2.5V.

If we connected an LED to this, we’d expect the brightness to be roughly half that if we had applied 5V.

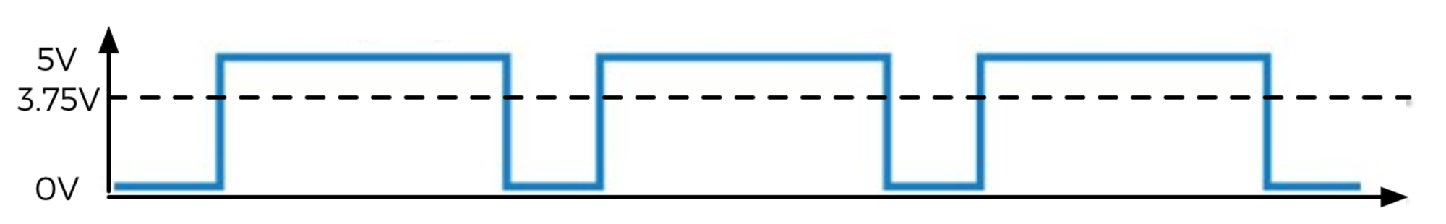
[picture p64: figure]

This PWM signal has a duty cycle of 75%. The average voltage is 75% of 5V (3.75V). On our LED, we’d expect the brightness to be slightly less than at 5V.

In this way we can output an analog voltage from a digital pin, meaning we can dim LEDs, control motor speed, and many more robot related shenanigans. This method is used everywhere, in fact it’s how your laptop dims the brightness of its screen!

To achieve this in our code, we do the following…

int pin, dutyCycle;

void setup(){

pinMode(pin, OUTPUT);

}

void loop(){

analogWrite(pin, dutyCycle);

}

To output a duty cycle of of 100%, we set dutyCycle = 255, for a duty cycle of 0%, we set dutyCycle = 0. For 50%, dutyCycle = 128 and so on.

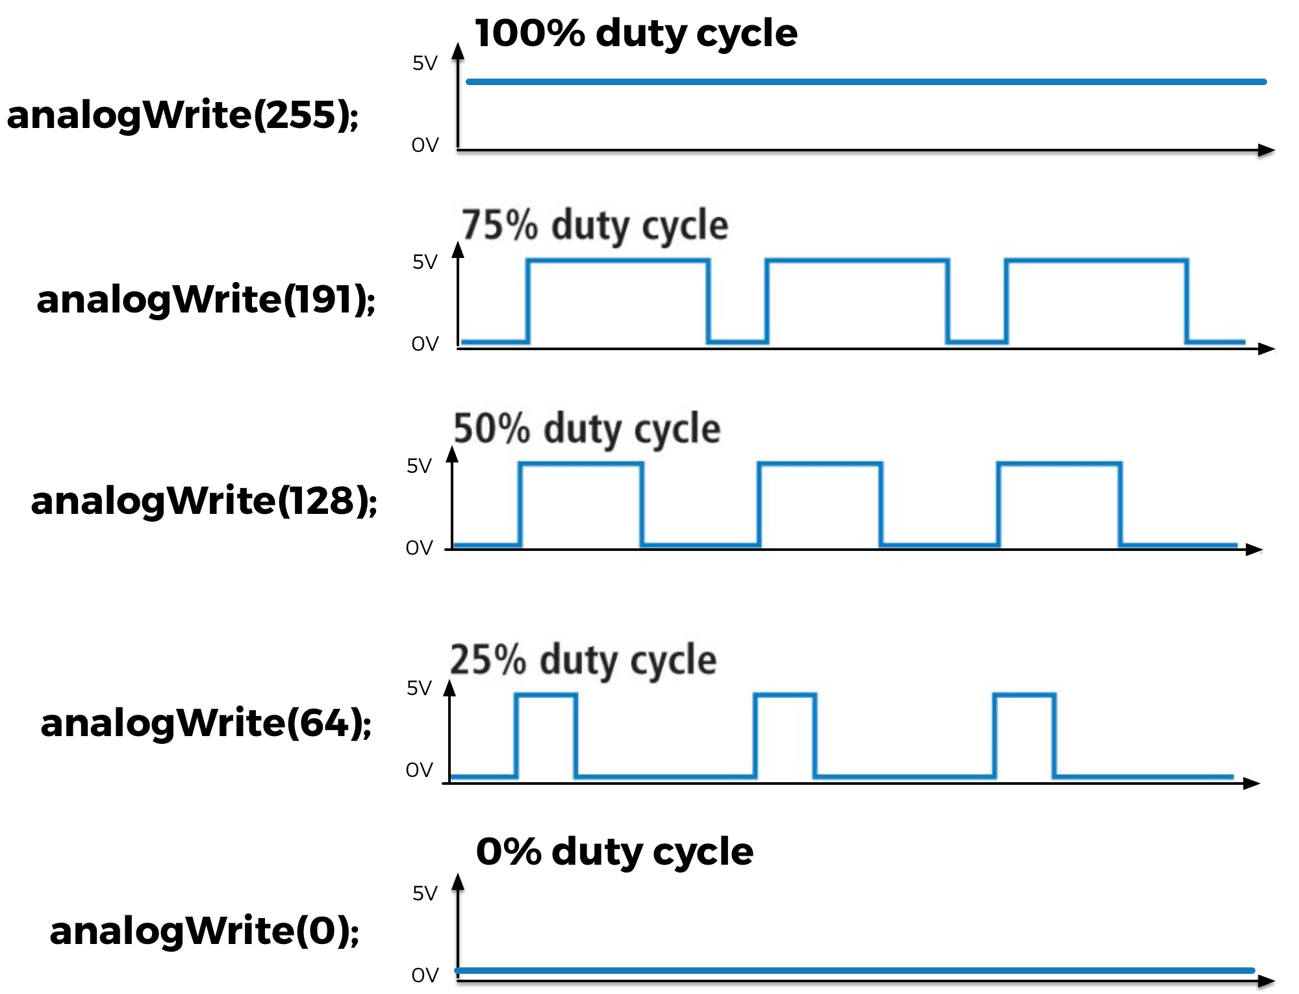
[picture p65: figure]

RIGHT BUTTON TEXT: Overview URL: engimake.com/coding/l1/0 | LEFT BUTTON TEXT: Servo Comms URL: engimake.com/coding/l1/2

URL: engimake.com/coding/l1/2

Servo Comms (H1)

Normal DC motors are simple. You apply a voltage, and the motor shaft spins with a speed corresponding to the voltage. Servo motors are different. They are designed to move to a specific angle, then hold that angle against all resistance. That’s why they’re so darn useful for legged robots like QuadBot.

To control them we use a special type of PWM signal from our microcontroller. This PWM signal uses a specific timing that the servo understands. The timing is a HIGH pulse between 1mS to 2mS.

A 1mS pulse means the servo shaft will turn to 0 degrees, whilst a 2mS pulse means the servo shaft will turn to 180 degrees.

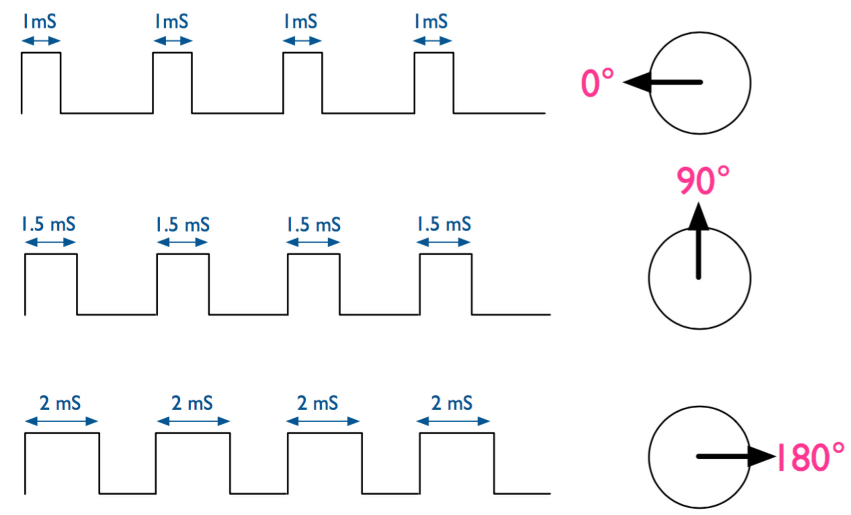
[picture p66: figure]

Thankfully we don’t need to worry the specifics because Arduino has a built in library for this.

To code this we write the following.

#include <Servo.h> //Include the servo library

Servo myServo; //Declares a servo called myServo

int pin, angle;

void setup(){

myServo.attach(pin) //Tell the program which pin the servo connects to

}

void loop(){

myServo.write(angle); //Send an angle to the servo

}
RIGHT BUTTON TEXT: Pulse Width Modulaion URL: engimake.com/coding/l1/1 | LEFT BUTTON TEXT: Serial Comms URL: engimake.com/coding/l1/3

URL: engimake.com/coding/l1/3

Serial Comms (H1)

Serial might sound like something you eat for breakfast, but the meaning here is quite different. Here serial means one after the other, like serial killer. Serial communication sends data by sending one bit after the other on a single pin.

Data is sent from the microcontroller by turning a digital pin on and off to signal each bit. It’s really no different from what we did to blink an LED, only faster and with a specific set of rules.

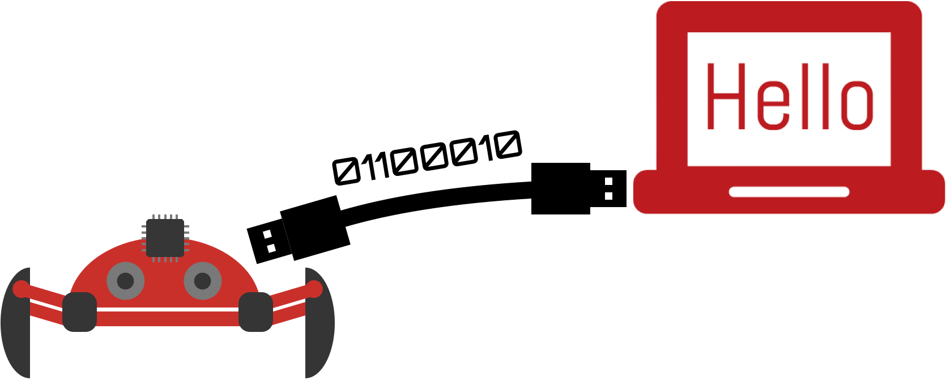
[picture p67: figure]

When the microcontroller sends eight bits in succession, that is a byte. Each 8-bit byte can store a character (a char data type).

We can send as many Chars as we like via serial communication to our computer, from the microcontroller. Here’s how we do it...

void setup(){

Serial.begin(9600); //Set up the serial port with 9600bps

}

void loop(){

Serial.print(“Hello Mr Roboto”); //Print the text to the serial port

}

The Serial.begin(9600) tells the microcontroller to get ready to send data with serial communication. 9600 is the speed of the data transfer in bits per second. Serial.print() sends the characters inside the quotes over the serial port, one by one. Each character needs 8 bits to be transmitted.

We can read this data on our computer by listening to the serial port. We can also send data from the computer to the microcontroller in a similar way.

Serial communication is very helpful when we’re debugging our code, or wanting to control the QuadBot from another device.
RIGHT BUTTON TEXT: Servo Comms URL: engimake.com/coding/l1/2 | LEFT BUTTON TEXT: Conclusion URL: engimake.com/coding/l1/4

URL: engimake.com/coding/l1/4

Conclusion (H1)

Now you’re fully schooled up in input and output, you’re ready to tackle programming QuadBot fully. Go check out the getting started guides!
RIGHT BUTTON TEXT: Serial Comms URL: engimake.com/coding/l1/3

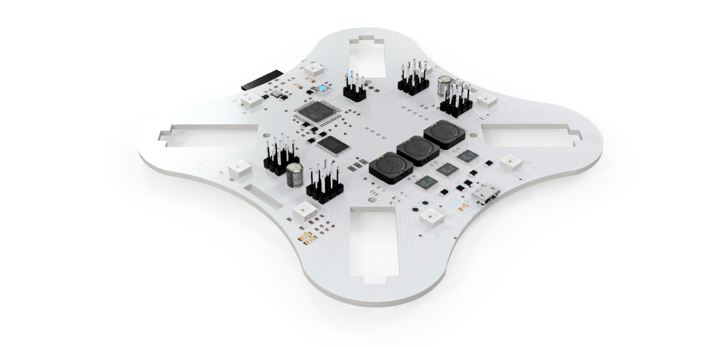
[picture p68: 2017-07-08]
Images/MakeBot (Exploded) v1.png

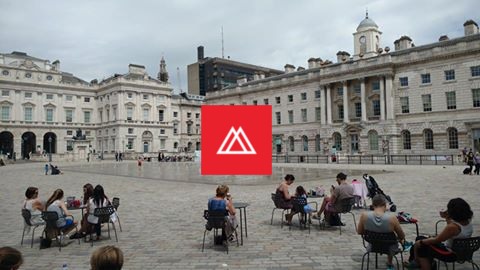
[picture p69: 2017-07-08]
Images/makerversity.png

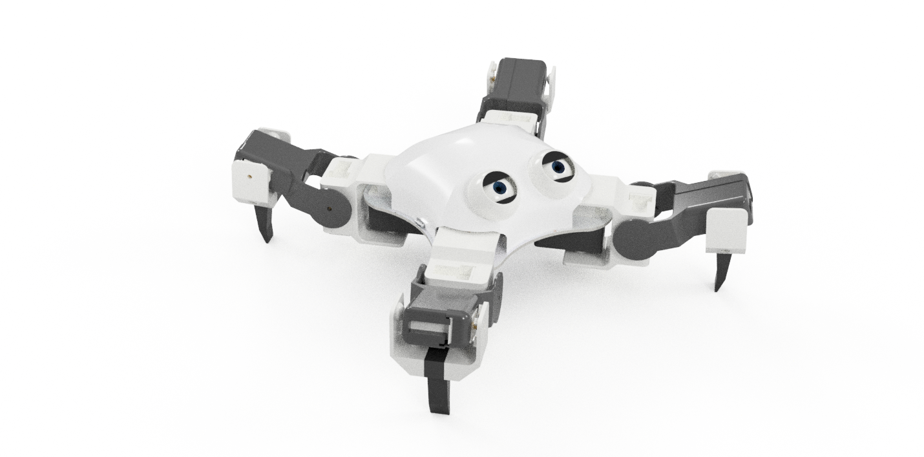
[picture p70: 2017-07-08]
Images/MakeBot (V2 Legs) v1.png

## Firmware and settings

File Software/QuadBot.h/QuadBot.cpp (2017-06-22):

/*
	QuadBot.cpp - Library that provides controlling functions for the QuadBot 
	(see comments in each function for details). 
	QuadBot is made by and a trademark of EngiMake.
	Created by Dan Elijah, May 01, 2017.
  	Released into the public domain.
  	Version 1 (first release).
  	
  	Please make sure you also include the Servo.h and Adafruit_NeoPixel.h 
  	libraries to your sketchbook before running this.
*/

#include "QuadBot.h"

Servo MA0;
Servo MA1;
Servo MB0;
Servo MB1;
Servo MC0;
Servo MC1;
Servo MD0;
Servo MD1;

Adafruit_NeoPixel pixels = Adafruit_NeoPixel(4, 7, NEO_GRB + NEO_KHZ800);  
Adafruit_NeoPixel strip = Adafruit_NeoPixel(4, 7, NEO_GRB + NEO_KHZ800);

/*
You can attach 1 extra motor to each leg.
Servo MA2;
Servo MB2;
Servo MC2;
Servo MD2;
*/ 
// %%%%%%%%%%%%%	DEFAULT VALUES	%%%%%%%%%%%%%%
int Bright = 255, ProcessDelay = 5000;
bool NoTone = false;
int angleMin = 59;
int angleMax = 147;
//%%%%%%%%%%%%%%%%%%%%%%%%%%%%%%%%%%%%%%%%%%%%%%%%

// int R1, G1, B1;
void QuadBot::begin() {

// Analog pins - directions
	pinMode(A0, OUTPUT);	// Piezo Buzzer
	pinMode(A1, INPUT);		// IR Reciever
	pinMode(A2, INPUT);		// Potentiometer Input
	// MD2.attach(A3);	// Motor D2 (Use the servo.attach command to inisialise the servo pins)
	MD1.attach(A4);	// Motor D1
	MD0.attach(A5);	// Motor D0
	
	// Digital pins - directions
	pinMode(0, INPUT);		// Serial Rx 
	pinMode(1, OUTPUT);		// Serial Tx
	// pinMode(2, ); User defined
	// pinMode(3, ); User defined 
	// MB2.attach(4);		// Motor B2
	MC1.attach(5);		// Motor C1
	MB0.attach(6);		// Motor B0
	pinMode(7, OUTPUT);		// RGB LED control
	pinMode(8, INPUT);		// Button input
	pinMode(9, OUTPUT);		// IR LED control
	MC0.attach(10);	// Motor C0
	// pinMode(11, ); User defined // Breakout pin 1 (next to 5V)
	MB1.attach(12);	// Motor B1
	// MC2.attach(13);	// Motor C2
	// MA2.attach(14);	// Motor A2
	MA0.attach(15);	// Motor A0
	MA1.attach(16);	// Motor A1
	
	beginAngle = 90;
	MA0.write(beginAngle);
	MA1.write(beginAngle);
	// MA2.write(beginAngle); // Only use Mx2 if you add extra motors.
	MB0.write(beginAngle);
	MB1.write(beginAngle);
	// MB2.write(beginAngle);
	MC0.write(beginAngle);
	MC1.write(beginAngle);
	// MC2.write(beginAngle);
	MD0.write(beginAngle);
	MD1.write(beginAngle);
	pixelCounter = 0; // A Starting counter for assigning multiple pixel assignment.
	// MD2.write(beginAngle);
	pixels.setPixelColor(0, pixels.Color(0,0,0));
	pixels.setPixelColor(1, pixels.Color(0,0,0));
	pixels.setPixelColor(2, pixels.Color(0,0,0));
	pixels.setPixelColor(3, pixels.Color(0,0,0));
	pixels.show();
}

void QuadBot::SetMotor(char MotorNumber, int angle) {
/*
Here we write the angle numbers to specific motors. The motors are objects by the
Servo library.
Input MotorNumber M0-M7, (M0 = the proximal motor on A)
Input angles from 0 to 90;
*/
//MotorNumber = str(MotorNumber);
//int angleMin = 59;
//int angleMax = 147;
// 0   min 28  max  180
int angle0 = constrain(angle, 28, 180);  
int angle1 = constrain(angle, 51, 140);
	switch (MotorNumber) {
		case char ('M0'):
			MA0.write(angle0);
			break;
		case char ('M1'):
			MA1.write(angle1);
			break;
		case char ('M2'):
			MB0.write(angle0);
			break;
		case char ('M3'):
			MB1.write(angle1);
			break;
		case char ('M4'):
			MC0.write(angle0);
			break;
		case char ('M5'):
			MC1.write(angle1);
			break;
		case char ('M6'):
			MD0.write(constrain(angle, 28, 130));
			break;
		case char ('M7'):
			MD1.write(angle1);
			break;
	/* The disignations below are for extra servos. Only add this code if you have 
	added new servos.
		case char('M8'):
			MC0.write(angle);
			break;
		case char('M9'):
			MC1.write(angle);
			break;
		case char('M10'):
			MD0.write(angle);
			break;
		case char('M11'):
			MD1.write(angle);
			break;
	*/
	}
	delayMicroseconds(ProcessDelay);
}

int QuadBot::LightRead(boolean readLED) {
	/*
	Here we record light from the IR reciever with the IR diode either on or 
	off. If the reading from the reciever changes (it reads lower for 
	increases in brigtness) between IR diode on and off then something is nearby
	and refrlecting light back at QuadBot. Use this for distance sensing. 
	*/
	if (readLED) {
		digitalWrite(9, HIGH);
	}
	else {
		digitalWrite(9, LOW);
	}
	return analogRead(A1);
}

boolean QuadBot::ReadButton() {
	/* Reads the input from the button
	output is reversed to read 0 off 1 on.
	*/
	return !digitalRead(8);
}

void QuadBot::SetBrightness(int Brightness) {
	/*
	This function changes the Bright value (default set at 255) to whatever the 
	user wants. It will reduce the RGB values equally by a factor of (255-x). 
	Setting brightness at 255 will give no dimming.
	NB/ For better dimming, consider using PWM (PWM(7, vlaue)).
	*/
	Bright = Brightness;
}

void QuadBot::SetLED(int NumLED, int R, int G, int B) {
	/*
	Function for lighting a given LED (NumLED) with an R G B color
	*/
	int R_1 = R - (255 - Bright); 
	if (R_1<0) {R_1=0;}
	int G_1 = G - (255 - Bright); 
	if (G_1<0) {G_1=0;}
	int B_1 = B - (255 - Bright); 
	if (B_1<0) {B_1=0;}
	
	pixels.setPixelColor(NumLED, pixels.Color(R_1, G_1, B_1));
	pixels.show();
	delayMicroseconds(ProcessDelay);
}

void QuadBot::SetLEDs(int R, int G, int B) {
	/*
	This Function lights all 4 LEDs with an R G B color.
	*/
	int R_1 = R - (255 - Bright); 
	if (R_1<0) {R_1=0;}
	int G_1 = G - (255 - Bright); 
	if (G_1<0) {G_1=0;}
	int B_1 = B - (255 - Bright); 
	if (B_1<0) {B_1=0;}
	
	pixels.setPixelColor(pixelCounter, pixels.Color(R_1,G_1,B_1));
	pixels.show();
	pixelCounter++;
	if (pixelCounter>4)	{pixelCounter=0;}
	delayMicroseconds(ProcessDelay);
}

void QuadBot::SetTone(int freq) {
	/*
	Sets and plays a tone of specified frequency.
	*/
	if (!NoTone) {
		tone(A0, freq);
	}
}

void QuadBot::StopTone() {
	/*
	Stops tones playing from the QuadBot.
	*/
	noTone(A0);
	// NoTone = true;
}

int QuadBot::ReadDial() {
	/*
	Reads the analog output from the dial.
	*/
	return analogRead(A2);
}

uint32_t QuadBot::Wheel(byte WheelPos) {
	/*
	Inputs a value from 0 to 255 and returns a HEX color value within a 
	graduated scale (R - G - B - R)
	*/
	WheelPos = 255 - WheelPos;
	if (WheelPos < 85) {
    	return pixels.Color(255 - WheelPos * 3, 0, WheelPos * 3);
  	}
  	if(WheelPos < 170) {
    	WheelPos -= 85;
    	return pixels.Color(0, WheelPos * 3, 255 - WheelPos * 3);
  	}
  	WheelPos -= 170;
  	return pixels.Color(WheelPos * 3, 255 - WheelPos * 3, 0);
}

int QuadBot::WheelR(byte WheelPos) {
	/*
	Inputs a value from 0 to 255 and returns a RED value for a color wheel 
	(R G B R).
	*/
	WheelPos = 255 - WheelPos;
	int col;
	if (WheelPos < 85) {
		col = (255 - WheelPos * 3);
		if (col < 0) {col = 0;}
    	return col;
  	}
  	if (WheelPos < 170) {
    	WheelPos -= 85;
    	return 0;
  	}
  	WheelPos -= 170;
  	col = (WheelPos * 3);
  	if (col < 0) {col = 0;}
  	return col;
}
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

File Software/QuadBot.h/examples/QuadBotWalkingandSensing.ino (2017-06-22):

/* QuadBot Walking example
  
  This example shows the walking and sensing functions of the QuadBot. It walks foward
  constantly sensing objects in its path by using the front LED and light sensor. When 
  something is detected, it turns 180 degrees and walks away.  
  
  The sequence includes:
  %%%%%  PRESS BUTTON TO START  %%%%%
  - Walk forwards
  - Use IR Sensor to detect obsticals in front of QuadBot.
  - When obstical is detected, rotate about 180 degrees clockwise.
  - Walk forwards again and repeat
  - For the 4th obstical, stay still and wait for button to be pushed to start routine again.
  
  Please note that due to small errors in leg movements, the QuadBot may drift to the left or 
  right. 
  
  Created 05 May 2017 by D Elijah.
  This code is in the public domain. Feel free to alter and improve.
  QuadBot is made by and a trademark of Engimake
*/

#include <Servo.h>
#include <Adafruit_NeoPixel.h>
#include <QuadBot.h>

QuadBot quadBot;

int i, button, n, reading; // i increases and gets reset for easch walking pattern
// button stores the input from the button
// n increases as light is being measured
// reading stores the light reading.

// threshold is the obstruction thereshold. Increasing this means QuadBot must get closer 
// to an obstruction to detect it.
int threshold = 25;
// This is 0 when there is no object and 1 when an object is in front of the QuadBot.
int obstruct;
// delayTime controls the speed of walking, turnCount increases by 1 for every turn.
int delayTime = 150, turnCount = 0;
// These variables stro light readings and calculate the averge light levels.
long int readlightOFF = 0, readlightON = 0, meanlightOFF, meanlightON;

void setup() {
  quadBot.begin(); // Initilse the settings for the QuadBot.
  Serial.begin(9600);
}

void loop() {  
  holdingFunction(button); // Press the button to start the program.
  turnCount = 0;
  //obstruct = distanceCalc(threshold);
  //Serial.println(number);
  while (true) {
    obstruct = distanceCalc(threshold);
    if (obstruct == 0) { // No obstructions
      quadBot.WalkForward(delayTime);
    }
    else {
      for (i=0;i<7;i++) {
        quadBot.RotateCW(delayTime/4);
      }
      turnCount++;
    }
    if (turnCount > 3) {
      quadBot.StandStill();
      delay(delayTime*2);
      break;
    }
  }
}

/// %%%%% EXTRA FUNCTIONS ARE BELOW %%%%%

int distanceCalc(int threshold) {
  readlightOFF = 0; 
  readlightON = 0; //Reset these values to 0.
  // quadBot.LightRead(false);
  
  quadBot.LightRead(HIGH);
  for (n=0;n<100;n++) {
    // Take a reading with the IR LED ON
    reading = quadBot.LightRead(HIGH);
    //take the sum of the readings.
    readlightOFF = readlightOFF + reading;
  }
  
  delay(10);
  
  quadBot.LightRead(LOW);
  for (n=0;n<100;n++) {
    // Take a reading with the IR LED OFF
    reading = quadBot.LightRead(LOW);
    // Take the sum of the readings.
    readlightON = readlightON + reading;
  }
  
  quadBot.LightRead(LOW); // Turn the LED off.
  
  meanlightOFF = readlightOFF/n; // Take the average light level with no LED.
  meanlightON = readlightON/n; // Take the average light level with LED.
  // If there is a difference > threshold then there is an object reflecting 
  // light back at the sensor
  if ( (meanlightON - meanlightOFF) > threshold ) {
    return 1;
  }
  else {
    return 0;
  }
}

// 
void holdingFunction(int button) {
  if (button == 0) { 
    // Button not pressed
    while (true) {
      // This holds the program untill you press the button 
      button = quadBot.ReadButton();
      if (button > 0) {
        break;
      }
    }
  }
}

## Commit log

2017-07-08 Learning resources + images
    Addition of learning resources and images
    [1 x Battery Holder (ANY).stl, 1 x Shell (WHITE).stl, 2 x Eye Part 1 (BLACK).stl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]
2017-07-08 Addition of new resources
    New resources
    [Bill of Materials + Placement Data.xlsx, Eye Base (x2).f3d, Eye Base (x2).iges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]
